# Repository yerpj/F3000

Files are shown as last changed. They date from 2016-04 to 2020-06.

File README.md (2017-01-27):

Power Unit 
----------------

This project aims at designing a generic power IO board for automotive projects

It features:
- 10x 12[V] digital inputs (fully filtered and protected)
- 1x lowside NTC conditionning circuit
- 1x full bridge power output (12V/13A) with temperature protection
- 2x isolated power relay outputs (12V/300mA) with voltage/current spike protection

The headers are meant to be project-agnostic and easy to wire

The interface voltage can be 3.3[V] or 10[V]

More info on demand

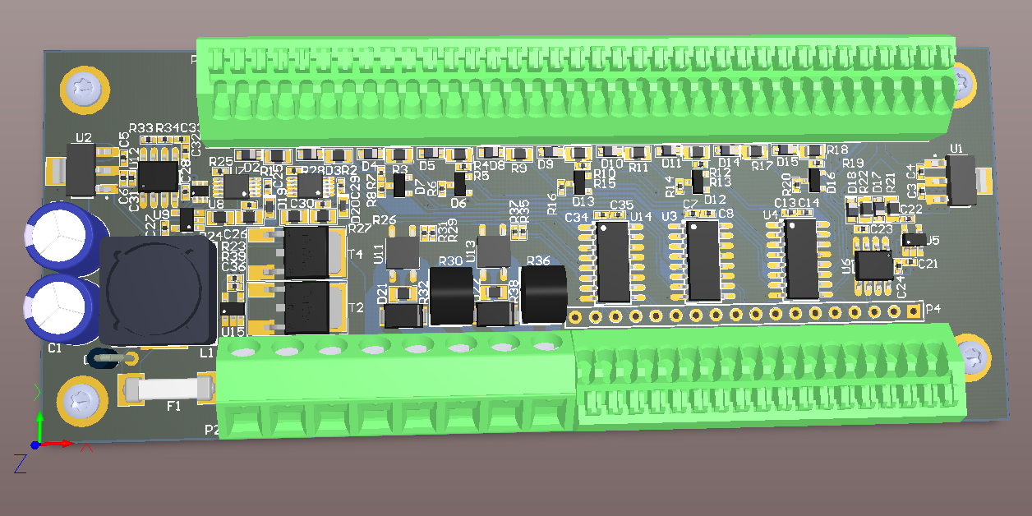
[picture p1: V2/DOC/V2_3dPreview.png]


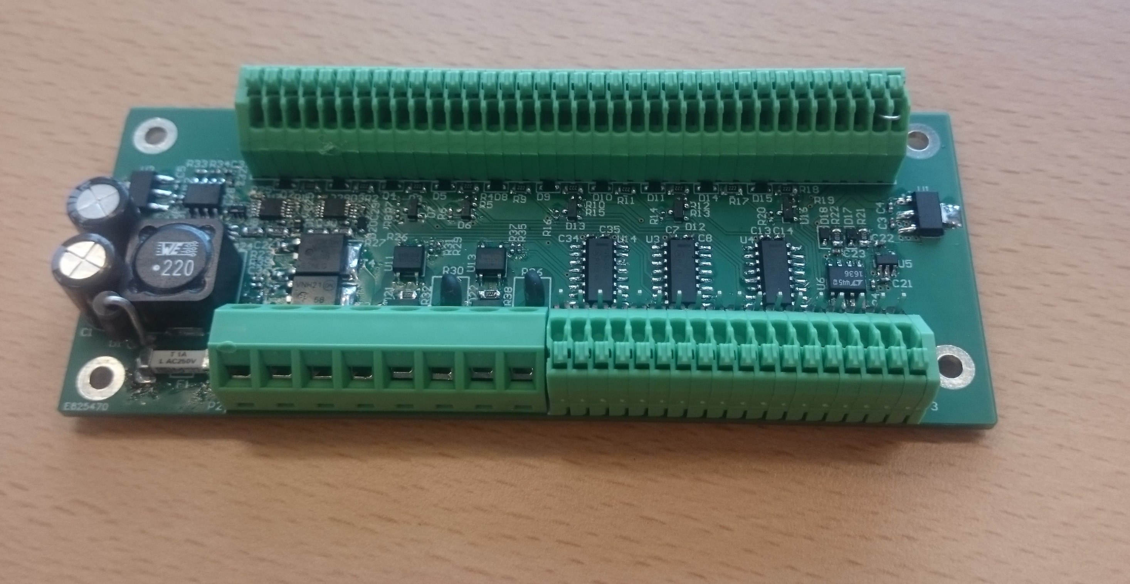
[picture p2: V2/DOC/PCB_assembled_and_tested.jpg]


Control Unit
----------------

As an integral part of the steering wheel, this control unit is able to monitor and drive every IO from the Power Unit, as well as the user interface.

It features:
- 10x 12[V] digital inputs 
- 3x digital outputs
- 6x pushbuttons inputs (SW debounced)
- 1x 7-seg display
- 21 LEDs forming a beautiful bargraph-style regime speed indicator
- individual LEDs for motor temperature, oil warning, neutral-position indication and driving mode*

*: The pilot can at any time select the best gear-driving mode:
- manual control: The gearbox is controlled by pallets on the steering wheel, foot-controlled declutching
- semi-automatic: The gearbox is controlled by pallets on the steering wheel, automatic declutching
- automatic: The gearbox is automatically driven according to engine speed for ascending gears engagement, and manually controlled for descending gears engagement

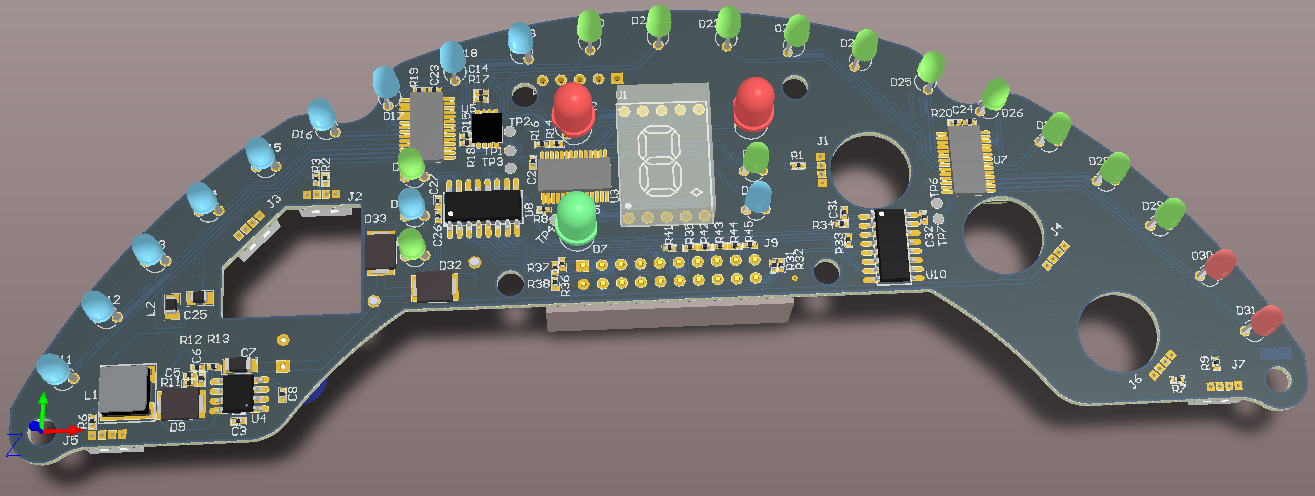
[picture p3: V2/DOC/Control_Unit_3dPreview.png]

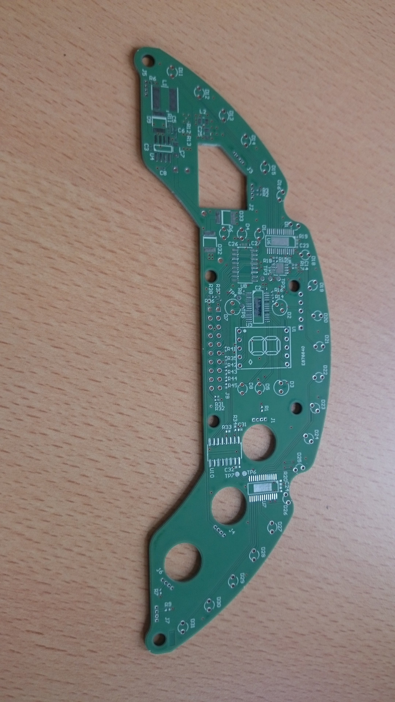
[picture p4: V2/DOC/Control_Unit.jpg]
  
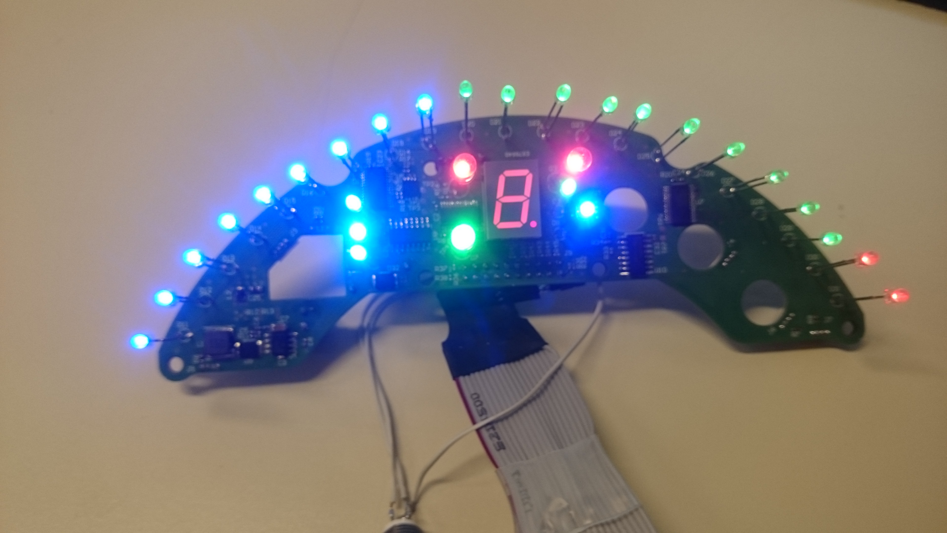
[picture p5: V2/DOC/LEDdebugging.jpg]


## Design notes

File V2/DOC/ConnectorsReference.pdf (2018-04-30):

CU | Spiral cords | PU
Cable | WU side | | PU side | P3 | P1 | P2
"Interface" | wire color | | wire color | "Interface" | "Inputs" | "Outputs"
Pin | Name | left | right | | left | right | Pin | Name | Pin | Name | Pin | Name | Wire
1 | VIN (12V) | | rouge | | | noir | 1 | GND (0V) | 1 | P1 | 1 | STOP+ | 6
2 | GND (0V) | | noir | | | rouge | 2 | VIN (12V) | 2 | GND (0V) | 2 | STOP- | 1
3 | NEUTRE | vert | | | | bleu | 3 | VNTC_out | 3 | VIN (12V) | 3 | START+ | 3
4 | START | jaune | | | | blanc | 4 | Res_out | 4 | P2 | 4 | START- | 1
5 | REGIME | | rose | | | rose | 5 | Regime_out | 5 | GND (0V) | 5 | MOT DC+ | 4
6 | TEMP | | bleu | | | brun | 6 | Huile_out | 6 | VIN (12V) | 6 | MOT DC- | 5
7 | RESERVED1 | | blanc | | blanc | | 7 | Embray_out | 7 | Rapport+ | 7 | VIN (12V) | 1
8 | | | | | rouge | | 8 | Gaz_out | 8 | GND (0V) | 8 | GND (0V) | 2
9 | HUILE | | brun | | vert | | 9 | Neutre_out | 9 | VIN (12V)
10 | EMBRAY | blanc | | | noir | | 10 | Rapport-_out | 10 | Rapport-
11 | SHIFTER | brun | | | rose | | 11 | Rapport+_out | 11 | GND (0V)
12 | CAME | gris | | | brun | | 12 | Shifter_out | 12 | VIN (12V)
13 | RESERVED2 | | gris | | gris | | 13 | Came_out | 13 | Neutre
14 | MOT- | | vert | | | jaune | 14 | Mot+_in | 14 | GND (0V)
15 | RESERVED3 | | | | | vert | 15 | Mot-_in | 15 | VIN (12V)
16 | MOT+ | | jaune | | jaune | | 16 | Relay1_in(Start) | 16 | Gaz
17 | RAPPORT+ | rose | | | bleu | | 17 | Relay2_in(Stop) | 17 | GND (0V)
18 | STOP | bleu | | | | | 18 | | 18 | VIN (12V)
19 | RAPPORT- | noir | | | | | | | 19 | Embray
20 | GAZ | rouge | | | | | | | 20 | GND (0V)
| | | | | | | | | 21 | VIN (12V)
| | | | | | | | | 22 | Huile
| | | | | | | | | 23 | GND (0V)
| | | | | | | | | 24 | VIN (12V)
| | | | | | | | | 25 | Régime
| | | | | | | | | 26 | GND (0V)
| | | | | | | | | 27 | VIN (12V)
| | | | | | | | | 28 | Res_in
| | | | | | | | | 29 | GND (0V)
| | | | | | | | | 30 | VIN (12V)
| | | | | | | | | 31 | NTC
| | | | | | | | | 32 | GND (0V)
| | | | | | | | | 33 | VIN (12V)
| | | | | | | | | 34 | 10V
| | | | | | | | | 35 | VIF
| | | | | | | | | 36 | 3.3V

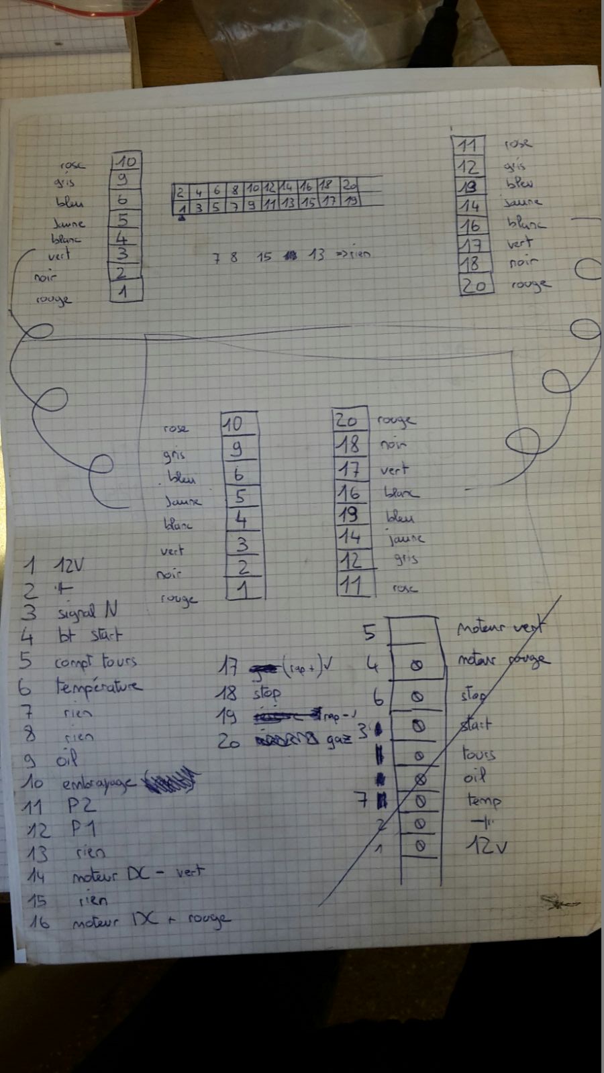
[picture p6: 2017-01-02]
V2/DOC/cablage_notes_julien1.jpg

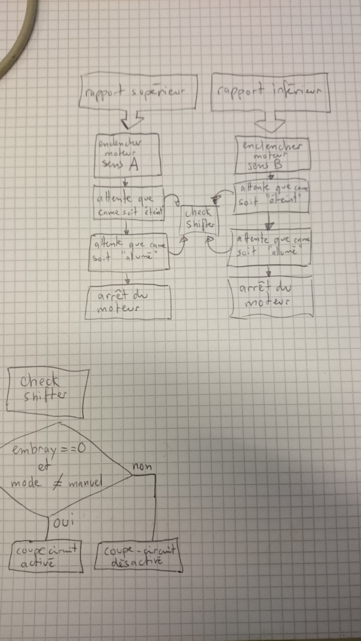
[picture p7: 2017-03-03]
V2/DOC/gear_up_down_procedure.jpeg

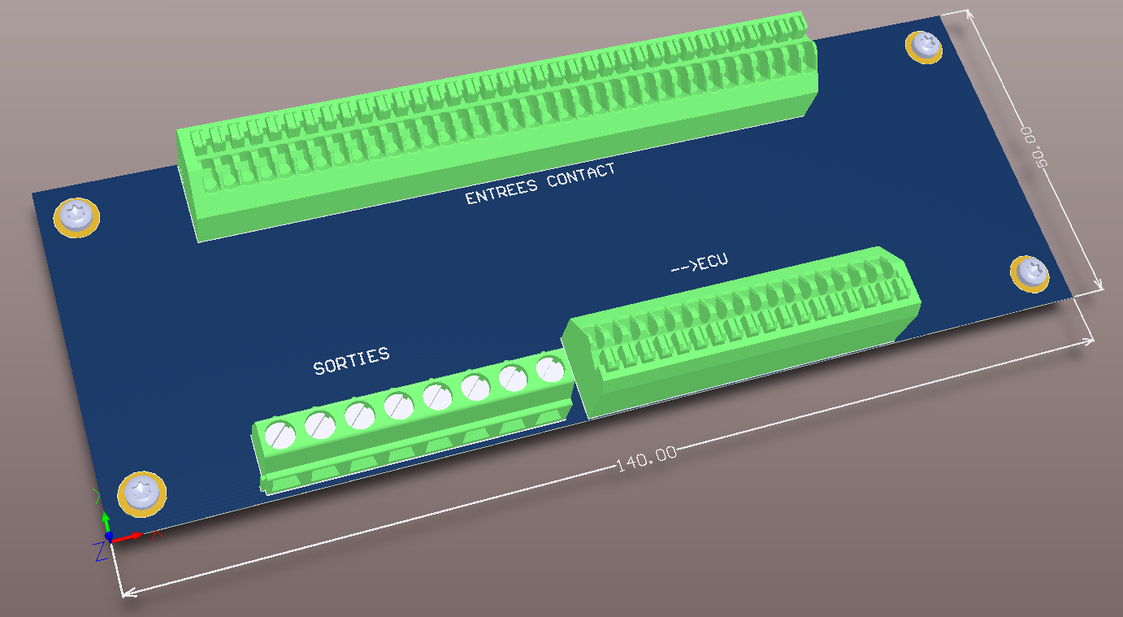
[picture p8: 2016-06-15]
V2/DOC/Capture d'écran 2016-06-15 20.59.19.png

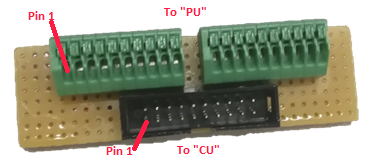
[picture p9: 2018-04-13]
V2/DOC/pics/WU.png

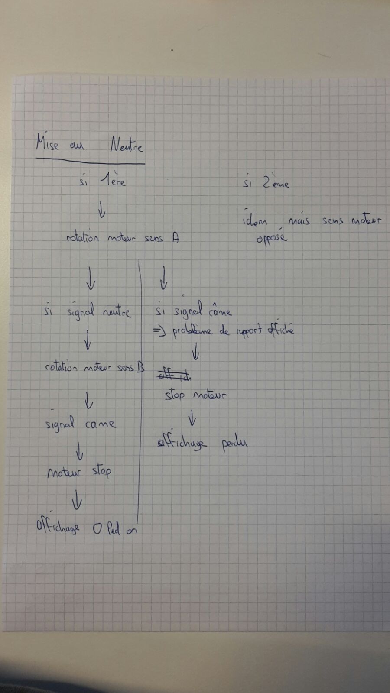
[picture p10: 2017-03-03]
V2/DOC/toNeutral_procedure.jpeg

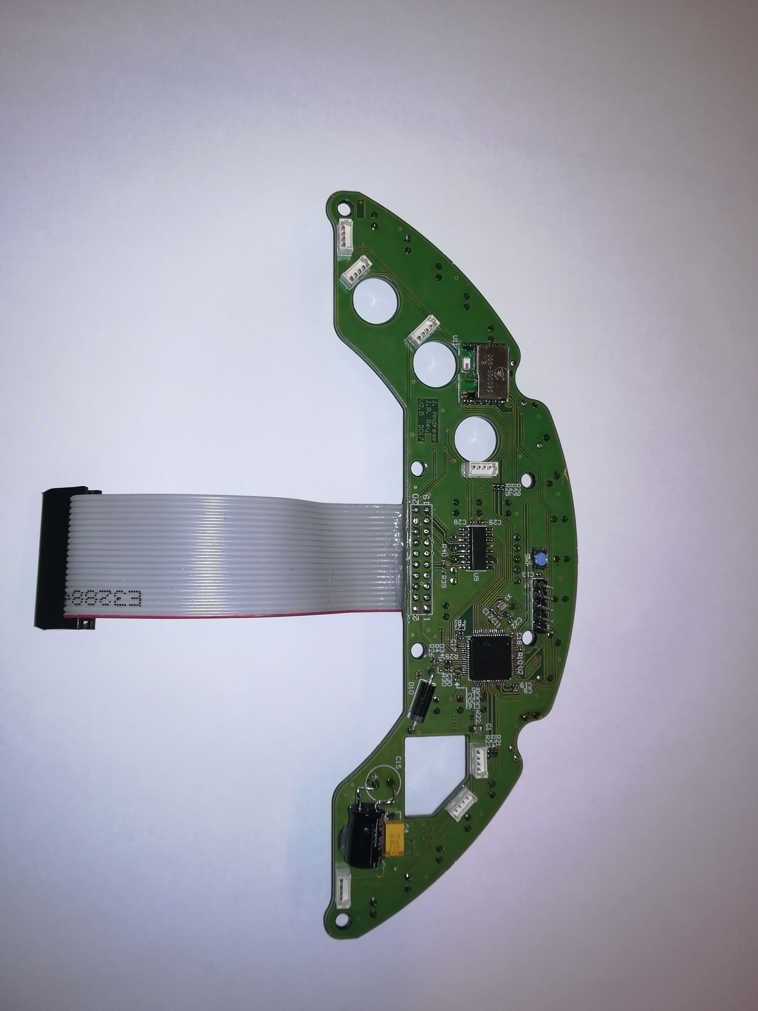
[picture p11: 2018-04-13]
V2/DOC/pics/2018-04-12 16.57.27.jpg

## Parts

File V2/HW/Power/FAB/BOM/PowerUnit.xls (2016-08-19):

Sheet: BOM Report
 |  |  |  | <Parameter Author Field=ProjectName Field=Revision not found>
 |  |  |  | Printed: | 2016-08-19
Index | Designator | Value | Footprint | Manufacturer | Manufacturer PartNum | Quantity
 | C1, C2 | 100u | C_pol8x12mm | Nichicon | UVR1H101MPD1TD | 2
 | C3, C4, C5, C6, C21, C22, C23 | 1u | 0402_ | Murata | GRM155R61E105MA12D | 7
 | C7, C8, C13, C14, C24, C26, C27, C28, C30, C31, C32, C33, C34, C35, C36 | 100n | 0402_ | TDK Corp. | C1005X5R1E104K050BC | 15
 | C9, C10, C11, C12, C15, C16, C17, C18, C19, C20, C37, C38, C39, C40 | 68n | 0603_ | Samsung | CL10B683KB8NNNC | 14
 | C25, C29 | 47n | 0402_ | Murata | GRM155R71H473KE14D | 2
 | D1 |  | R_DIL_vertical_holes1_2mm | ON Semi | 1N5354BG | 1
 | D2, D3, D4, D5, D8, D9, D10, D11, D14, D15, D17, D18 |  | SOD323 | Micro Commercial Co | 1N4148WX-TP | 12
 | D6, D7, D12, D13, D16 |  | SOT23 | Diodes Inc. | AZ23C15-7-F | 5
 | D19, D20 |  | 0603_Pol | Comchip Tech. | CDSU4148 | 2
 | D21, D22 |  | DO-214AC | Littelfuse Inc | SMAJ24CA | 2
 | F1 |  | FUSE_UMT250 | Schurter Inc | 3403.0166.11 | 1
 | L1 | 22u | WURTH_7447709220 | Wurth Electronics Inc | 7447709220 | 1
 | P1 |  | PHOENIX_PTSA05_36 | Phoenix Contact | 1990164 | 1
 | P2 |  | PHOENIX_SMKDSN8 | Phoenix | 1869279 | 1
 | P3 |  | PHOENIX_PTSA05_18 | Phoenix | 1990164 | 1
 | P4 |  | HDR1X18 |  |  | 1
 | R1, R2, R3, R4, R9, R10, R11, R12, R17, R18 | 2k2 | 0805_ | Yageo | RC0805JR-072K2L | 10
 | R5, R6, R7, R8, R13, R14, R15, R16, R19, R20, R31, R33, R37, R39, R40, R41, R42, R43 | 10k | 0402_ | Panasonic | ERJ-2RKF1002X | 18
 | R21, R22 | 500R | 0805_ | Yageo | RC0805FR-07510RL | 2
 | R23, R24, R26, R27 | 22R | 0805_ | Panasonic | ERJ-6ENF22R0V | 4
 | R25, R28 | 100k | 0402_ | Susumu | RR0510P-104-D | 2
 | R29, R35 | 680R | 0402_ | Panasonic | ERJ-2RKF6800X | 2
 | R30, R36 |  | MF72-010D5 | Cantherm | MF72-060D5 | 2
 | R32, R38 | 22k | 0805_ | Rohm Semi | ESR10EZPJ223 | 2
 | R34 | 1k | 0402_ | Rohm Semi | MCR01MRTF1001 | 1
 | T1, T2, T3, T4 |  | DPAK | On Semi | NTD5867NLT4G | 4
 | U1 |  | SOT223-4M | Microchip | MCP1804T-A002I/DB | 1
 | U2 |  | SOT223-4M | Microchip | MCP1804T-3302I/DB | 1
 | U3, U4, U14 |  | SOIC16 | On Semi | MC14504BDG | 3
 | U5 |  | sot23-5 | Microchip | MCP1804T-5002I/OT | 1
 | U6 |  | soic8 | Linear Technology | LT1636CS8#PBF | 1
 | U7, U10 |  | VSSOP10 | Texas Intruments | LM5106MM/NOPB | 2
 | U8 |  | SOT363 | Diodes Inc. | 74LVC1G11DW-7 | 1
 | U9 |  | SOT353 | Diodes Inc. | 74AHC1G32SE-7 | 1
 | U11, U13 |  | CPC10xxN | IXYS Integrated | CPC1018NTR | 2
 | U12 |  | soic8 | Texas Intruments | TLC555CDR | 1
 | U15 |  | SOT23-5 | Microchip | MCP9501PT-095E/OT | 1

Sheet: Project Information
Project Full Path | C:\Users\jeanphil.rey\Documents\JP\Perso\F3000\F3000git\V2\HW\Power\PowerUnit.PrjPCB
Project Filename | PowerUnit.PrjPCB
Variant Name | None
Data-Source Filename | PowerUnit.PrjPCB
Data-Source Full Path | C:\Users\jeanphil.rey\Documents\JP\Perso\F3000\F3000git\V2\HW\Power\PowerUnit.PrjPCB
Title | <Parameter Title not found>
Total Quantity | 130
Report Time | 16:50:49
Report Date | 19.08.2016
Report Date & Tine | 19.08.2016 16:50:49
Output Name | Bill of Materials
Output Type | BOM_PartType
Output Generator Name | BOM
Output Generator Description | Bill of Materials

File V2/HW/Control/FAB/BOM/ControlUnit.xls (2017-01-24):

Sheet: BOM Report
 | Novaccess S.A. Rue Galilée 6 CH-1400 Yverdon-les-Bains | ControlUnit.PrjPCB |  |  |  | Jean-Philippe Rey tel:+41 24 557 27 67
 |  |  |  |  |  | Printed: | 2017-01-24
 |  |  |  |  |  | Quantity: | 2
Entry | Designator | #Column Name Error:value | #Column Name Error:Manufacturer | #Column Name Error:Manufacturer PartNum | Footprint | Digikey ref | Quantity | Expanded Quantity
1 | C1, C25 |  |  |  | 0805_ | 490-10511-1-ND | 2 | 4
2 | C2, C3, C8, C13, C14, C17, C18, C19, C20, C21, C22, C23, C24, C26, C27, C28, C29, C31, C32 |  |  |  | 0402_ | 445-4964-1-ND | 19 | 38
3 | C4 |  |  |  | 2917 | 399-10524-1-ND | 1 | 2
4 | C5, C6 |  |  |  | 0402_ | 1276-1531-1-ND | 2 | 4
5 | C7 |  |  |  | 1206_ | 1276-2876-1-ND | 1 | 2
6 | C9, C10 |  |  |  | 0402_ | 490-10451-1-ND | 2 | 4
7 | C11, C12 |  |  |  | 0402_ | 1276-1608-1-ND | 2 | 4
8 | C15 |  |  |  | C_pol8x12mm | 493-5916-1-ND | 1 | 2
9 | C16, C30 |  |  |  | 0402_ | 490-5915-1-ND | 2 | 4
10 | D1, D5, D6, D20, D21, D22, D23, D24, D25, D26, D27, D28, D29 |  |  |  | LED3MM_GREEN | 754-1915-ND | 13 | 26
11 | D2, D3 |  |  |  | LED5MM_RED | C503B-RCN-CW0Z0AA1-ND | 2 | 4
12 | D4, D8, D11, D12, D13, D14, D15, D16, D17, D18, D19 |  |  |  | LED3MM_BLUE | 732-5011-ND | 11 | 22
13 | D7 |  |  |  | LED5MM_GREEN | 754-1920-ND | 1 | 2
14 | D9, D32, D33 |  |  |  | SMB_FLAT | 497-8036-1-ND | 3 | 6
15 | D10 |  |  |  | 1N5354 | 1N5354BGOS-ND | 1 | 2
16 | D30, D31 |  |  |  | LED3MM_RED | 732-5013-ND | 2 | 4
17 | FB1 |  |  |  | 0402_ | 490-3999-1-ND | 1 | 2
18 | J1, J2, J3, J4, J5, J6, J7 |  |  |  | MOLEX53047-0410 | WM1733-ND | 7 | 14
19 | J8 |  |  |  | HDR1X5 | A9BAG-0502F-ND | 1 | 2
20 | J9 |  |  |  | header2x10 |  | 1 | 2
21 | L1 |  |  |  | SRN6028 | SRN6028-150MCT-ND | 1 | 2
22 | L2 |  |  |  | 0805_ | 587-2903-1-ND | 1 | 2
23 | R1, R2, R3, R6, R7, R9 |  |  |  | 0402_ | RHM1.00KCDCT-ND | 6 | 12
24 | R5, R10, R31, R32, R33, R34, R35, R36, R37, R38, R39, R40, R41, R42, R43, R44, R45 |  |  |  | 0402_ | RR05P10.0KDCT-ND | 17 | 34
25 | R8, R19, R20 |  |  |  | 0402_ | 311-3KLRCT-ND | 3 | 6
26 | R11 |  |  |  | 0402_ | P27.0KLCT-ND | 1 | 2
27 | R12, R14, R15, R16, R17, R18 |  |  |  | 0402_ | P10.0KLCT-ND | 6 | 12
28 | R13 |  |  |  | 0402_ | P3.30KLCT-ND | 1 | 2
29 | R21, R22, R23, R24, R25, R27, R28 |  |  |  | 0402_ | 311-330JRCT-ND | 7 | 14
30 | R29 |  |  |  | 0402_ | 311-1.80KLRCT-ND | 1 | 2
31 | R30 |  |  |  | 0402_ | 311-3.30KLRCT-ND | 1 | 2
32 | SW1 |  |  |  | microswitch_PTS810 | CKN10502CT-ND | 1 | 2
33 | U1 |  |  |  | TDSR1350 | TDSR1350-ND | 1 | 2
34 | U2 |  |  |  | LQFP64 | 497-11154-ND | 1 | 2
35 | U3, U6, U7 |  |  |  | HTSSOP28 | 568-10954-1-ND | 3 | 6
36 | U4 |  |  |  | soic8 | 296-23902-1-ND | 1 | 2
37 | U5 |  |  |  | USON_8L | 1092-1056-ND | 1 | 2
38 | U8, U9, U10 |  |  |  | SOIC16 | MC14504BDGOS-ND | 3 | 6
39 | U11 |  |  |  | SPBT2632C2A | 497-13189-ND | 1 | 2
40 | X1 |  |  |  | FA_128 | 887-2000-1-ND | 1 | 2
41 |  |  |  |  |  |  |  | 0
42 |  |  |  |  |  |  |  | 0
43 |  |  |  |  |  |  |  | 0
44 |  |  |  |  |  |  |  | 0
45 |  |  |  |  |  |  |  | 0
46 |  |  |  |  |  |  |  | 0
47 |  |  |  |  |  |  |  | 0
48 |  |  |  |  |  |  |  | 0
49 |  |  |  |  |  |  |  | 0
50 |  |  |  |  |  |  |  | 0
51 |  |  |  |  |  |  |  | 0
52 |  |  |  |  |  |  |  | 0
53 |  |  |  |  |  |  |  | 0
54 |  |  |  |  |  |  |  | 0
55 |  |  |  |  |  |  |  | 0
56 |  |  |  |  |  |  |  | 0
57 |  |  |  |  |  |  |  | 0
58 |  |  |  |  |  |  |  | 0
59 |  |  |  |  |  |  |  | 0
60 |  |  |  |  |  |  |  | 0
61 |  |  |  |  |  |  |  | 0
62 |  |  |  |  |  |  |  | 0
63 |  |  |  |  |  |  |  | 0
64 |  |  |  |  |  |  |  | 0
65 |  |  |  |  |  |  |  | 0
66 |  |  |  |  |  |  |  | 0
67 |  |  |  |  |  |  |  | 0
68 |  |  |  |  |  |  |  | 0
69 |  |  |  |  |  |  |  | 0
70 |  |  |  |  |  |  |  | 0
71 |  |  |  |  |  |  |  | 0
72 |  |  |  |  |  |  |  | 0
73 |  |  |  |  |  |  |  | 0
74 |  |  |  |  |  |  |  | 0
75 |  |  |  |  |  |  |  | 0
76 |  |  |  |  |  |  |  | 0
77 |  |  |  |  |  |  |  | 0
78 |  |  |  |  |  |  |  | 0
79 |  |  |  |  |  |  |  | 0
80 |  |  |  |  |  |  |  | 0
81 |  |  |  |  |  |  |  | 0
82 |  |  |  |  |  |  |  | 0
83 |  |  |  |  |  |  |  | 0
84 |  |  |  |  |  |  |  | 0
85 |  |  |  |  |  |  |  | 0
86 |  |  |  |  |  |  |  | 0
87 |  |  |  |  |  |  |  | 0
88 |  |  |  |  |  |  |  | 0
89 |  |  |  |  |  |  |  | 0
90 |  |  |  |  |  |  |  | 0
91 |  |  |  |  |  |  |  | 0
92 |  |  |  |  |  |  |  | 0
93 |  |  |  |  |  |  |  | 0
94 |  |  |  |  |  |  |  | 0
95 |  |  |  |  |  |  |  | 0
96 |  |  |  |  |  |  |  | 0
97 |  |  |  |  |  |  |  | 0
98 |  |  |  |  |  |  |  | 0
99 |  |  |  |  |  |  |  | 0
100 |  |  |  |  |  |  |  | 0
101 |  |  |  |  |  |  |  | 0
102 |  |  |  |  |  |  |  | 0
103 |  |  |  |  |  |  |  | 0
104 |  |  |  |  |  |  |  | 0
105 |  |  |  |  |  |  |  | 0
106 |  |  |  |  |  |  |  | 0
107 |  |  |  |  |  |  |  | 0
108 |  |  |  |  |  |  |  | 0
109 |  |  |  |  |  |  |  | 0
110 |  |  |  |  |  |  |  | 0
111 |  |  |  |  |  |  |  | 0
112 |  |  |  |  |  |  |  | 0
113 |  |  |  |  |  |  |  | 0
114 |  |  |  |  |  |  |  | 0
115 |  |  |  |  |  |  |  | 0
116 |  |  |  |  |  |  |  | 0
117 |  |  |  |  |  |  |  | 0
118 |  |  |  |  |  |  |  | 0
119 |  |  |  |  |  |  |  | 0
120 |  |  |  |  |  |  |  | 0
121 |  |  |  |  |  |  |  | 0
122 |  |  |  |  |  |  |  | 0
123 |  |  |  |  |  |  |  | 0
124 |  |  |  |  |  |  |  | 0
125 |  |  |  |  |  |  |  | 0
126 |  |  |  |  |  |  |  | 0
127 |  |  |  |  |  |  |  | 0
128 |  |  |  |  |  |  |  | 0
129 |  |  |  |  |  |  |  | 0
130 |  |  |  |  |  |  |  | 0
131 |  |  |  |  |  |  |  | 0
132 |  |  |  |  |  |  |  | 0
133 |  |  |  |  |  |  |  | 0
134 |  |  |  |  |  |  |  | 0
135 |  |  |  |  |  |  |  | 0
136 |  |  |  |  |  |  |  | 0
137 |  |  |  |  |  |  |  | 0
138 |  |  |  |  |  |  |  | 0
139 |  |  |  |  |  |  |  | 0
140 |  |  |  |  |  |  |  | 0
141 |  |  |  |  |  |  |  | 0
142 |  |  |  |  |  |  |  | 0
143 |  |  |  |  |  |  |  | 0
144 |  |  |  |  |  |  |  | 0
145 |  |  |  |  |  |  |  | 0
146 |  |  |  |  |  |  |  | 0
147 |  |  |  |  |  |  |  | 0
148 |  |  |  |  |  |  |  | 0
149 |  |  |  |  |  |  |  | 0
150 |  |  |  |  |  |  |  | 0
151 |  |  |  |  |  |  |  | 0
152 |  |  |  |  |  |  |  | 0
153 |  |  |  |  |  |  |  | 0
154 |  |  |  |  |  |  |  | 0
155 |  |  |  |  |  |  |  | 0
156 |  |  |  |  |  |  |  | 0
157 |  |  |  |  |  |  |  | 0
158 |  |  |  |  |  |  |  | 0
159 |  |  |  |  |  |  |  | 0
160 |  |  |  |  |  |  |  | 0
161 |  |  |  |  |  |  |  | 0
162 |  |  |  |  |  |  |  | 0
163 |  |  |  |  |  |  |  | 0
164 |  |  |  |  |  |  |  | 0
165 |  |  |  |  |  |  |  | 0
166 |  |  |  |  |  |  |  | 0
167 |  |  |  |  |  |  |  | 0
168 |  |  |  |  |  |  |  | 0
169 |  |  |  |  |  |  |  | 0
170 |  |  |  |  |  |  |  | 0
171 |  |  |  |  |  |  |  | 0
172 |  |  |  |  |  |  |  | 0
173 |  |  |  |  |  |  |  | 0
174 |  |  |  |  |  |  |  | 0
175 |  |  |  |  |  |  |  | 0
176 |  |  |  |  |  |  |  | 0
177 |  |  |  |  |  |  |  | 0
178 |  |  |  |  |  |  |  | 0
179 |  |  |  |  |  |  |  | 0
180 |  |  |  |  |  |  |  | 0
181 |  |  |  |  |  |  |  | 0
182 |  |  |  |  |  |  |  | 0
183 |  |  |  |  |  |  |  | 0
184 |  |  |  |  |  |  |  | 0
185 |  |  |  |  |  |  |  | 0
186 |  |  |  |  |  |  |  | 0
187 |  |  |  |  |  |  |  | 0
188 |  |  |  |  |  |  |  | 0
189 |  |  |  |  |  |  |  | 0
190 |  |  |  |  |  |  |  | 0
191 |  |  |  |  |  |  |  | 0
192 |  |  |  |  |  |  |  | 0
193 |  |  |  |  |  |  |  | 0
194 |  |  |  |  |  |  |  | 0
195 |  |  |  |  |  |  |  | 0
196 |  |  |  |  |  |  |  | 0
197 |  |  |  |  |  |  |  | 0
198 |  |  |  |  |  |  |  | 0
199 |  |  |  |  |  |  |  | 0
200 |  |  |  |  |  |  |  | 0
201 |  |  |  |  |  |  |  | 0
202 |  |  |  |  |  |  |  | 0
203 |  |  |  |  |  |  |  | 0
204 |  |  |  |  |  |  |  | 0
205 |  |  |  |  |  |  |  | 0
206 |  |  |  |  |  |  |  | 0
207 |  |  |  |  |  |  |  | 0
208 |  |  |  |  |  |  |  | 0
209 |  |  |  |  |  |  |  | 0
210 |  |  |  |  |  |  |  | 0
211 |  |  |  |  |  |  |  | 0
212 |  |  |  |  |  |  |  | 0
213 |  |  |  |  |  |  |  | 0
214 |  |  |  |  |  |  |  | 0
215 |  |  |  |  |  |  |  | 0
216 |  |  |  |  |  |  |  | 0
217 |  |  |  |  |  |  |  | 0
218 |  |  |  |  |  |  |  | 0
219 |  |  |  |  |  |  |  | 0
220 |  |  |  |  |  |  |  | 0
221 |  |  |  |  |  |  |  | 0
222 |  |  |  |  |  |  |  | 0
223 |  |  |  |  |  |  |  | 0
224 |  |  |  |  |  |  |  | 0
225 |  |  |  |  |  |  |  | 0
226 |  |  |  |  |  |  |  | 0
227 |  |  |  |  |  |  |  | 0
228 |  |  |  |  |  |  |  | 0
229 |  |  |  |  |  |  |  | 0
230 |  |  |  |  |  |  |  | 0
231 |  |  |  |  |  |  |  | 0
232 |  |  |  |  |  |  |  | 0
233 |  |  |  |  |  |  |  | 0
234 |  |  |  |  |  |  |  | 0
235 |  |  |  |  |  |  |  | 0
236 |  |  |  |  |  |  |  | 0
237 |  |  |  |  |  |  |  | 0
238 |  |  |  |  |  |  |  | 0
239 |  |  |  |  |  |  |  | 0
240 |  |  |  |  |  |  |  | 0
241 |  |  |  |  |  |  |  | 0
242 |  |  |  |  |  |  |  | 0
243 |  |  |  |  |  |  |  | 0
244 |  |  |  |  |  |  |  | 0
245 |  |  |  |  |  |  |  | 0
246 |  |  |  |  |  |  |  | 0
247 |  |  |  |  |  |  |  | 0
248 |  |  |  |  |  |  |  | 0
249 |  |  |  |  |  |  |  | 0
250 |  |  |  |  |  |  |  | 0
251 |  |  |  |  |  |  |  | 0
252 |  |  |  |  |  |  |  | 0
253 |  |  |  |  |  |  |  | 0
254 |  |  |  |  |  |  |  | 0
255 |  |  |  |  |  |  |  | 0
256 |  |  |  |  |  |  |  | 0
257 |  |  |  |  |  |  |  | 0
258 |  |  |  |  |  |  |  | 0
259 |  |  |  |  |  |  |  | 0
260 |  |  |  |  |  |  |  | 0
261 |  |  |  |  |  |  |  | 0
262 |  |  |  |  |  |  |  | 0
263 |  |  |  |  |  |  |  | 0
264 |  |  |  |  |  |  |  | 0
265 |  |  |  |  |  |  |  | 0
266 |  |  |  |  |  |  |  | 0
267 |  |  |  |  |  |  |  | 0
268 |  |  |  |  |  |  |  | 0
269 |  |  |  |  |  |  |  | 0
270 |  |  |  |  |  |  |  | 0
271 |  |  |  |  |  |  |  | 0
272 |  |  |  |  |  |  |  | 0
273 |  |  |  |  |  |  |  | 0
274 |  |  |  |  |  |  |  | 0
275 |  |  |  |  |  |  |  | 0
276 |  |  |  |  |  |  |  | 0
277 |  |  |  |  |  |  |  | 0
278 |  |  |  |  |  |  |  | 0
279 |  |  |  |  |  |  |  | 0
280 |  |  |  |  |  |  |  | 0
281 |  |  |  |  |  |  |  | 0
282 |  |  |  |  |  |  |  | 0
283 |  |  |  |  |  |  |  | 0
284 |  |  |  |  |  |  |  | 0
285 |  |  |  |  |  |  |  | 0
286 |  |  |  |  |  |  |  | 0
287 |  |  |  |  |  |  |  | 0
288 |  |  |  |  |  |  |  | 0
289 |  |  |  |  |  |  |  | 0
290 |  |  |  |  |  |  |  | 0
291 |  |  |  |  |  |  |  | 0
292 |  |  |  |  |  |  |  | 0
293 |  |  |  |  |  |  |  | 0
294 |  |  |  |  |  |  |  | 0
295 |  |  |  |  |  |  |  | 0
296 |  |  |  |  |  |  |  | 0
297 |  |  |  |  |  |  |  | 0
298 |  |  |  |  |  |  |  | 0
299 |  |  |  |  |  |  |  | 0
300 |  |  |  |  |  |  |  | 0
301 |  |  |  |  |  |  |  | 0
302 |  |  |  |  |  |  |  | 0
303 |  |  |  |  |  |  |  | 0
304 |  |  |  |  |  |  |  | 0
305 |  |  |  |  |  |  |  | 0
306 |  |  |  |  |  |  |  | 0
307 |  |  |  |  |  |  |  | 0
308 |  |  |  |  |  |  |  | 0
309 |  |  |  |  |  |  |  | 0
310 |  |  |  |  |  |  |  | 0
311 |  |  |  |  |  |  |  | 0
312 |  |  |  |  |  |  |  | 0
313 |  |  |  |  |  |  |  | 0
314 |  |  |  |  |  |  |  | 0
315 |  |  |  |  |  |  |  | 0
316 |  |  |  |  |  |  |  | 0
317 |  |  |  |  |  |  |  | 0
318 |  |  |  |  |  |  |  | 0
319 |  |  |  |  |  |  |  | 0
320 |  |  |  |  |  |  |  | 0
321 |  |  |  |  |  |  |  | 0
322 |  |  |  |  |  |  |  | 0
323 |  |  |  |  |  |  |  | 0
324 |  |  |  |  |  |  |  | 0
325 |  |  |  |  |  |  |  | 0
326 |  |  |  |  |  |  |  | 0
327 |  |  |  |  |  |  |  | 0
328 |  |  |  |  |  |  |  | 0
329 |  |  |  |  |  |  |  | 0
330 |  |  |  |  |  |  |  | 0
331 |  |  |  |  |  |  |  | 0
332 |  |  |  |  |  |  |  | 0
333 |  |  |  |  |  |  |  | 0
334 |  |  |  |  |  |  |  | 0
335 |  |  |  |  |  |  |  | 0
336 |  |  |  |  |  |  |  | 0
337 |  |  |  |  |  |  |  | 0
338 |  |  |  |  |  |  |  | 0
339 |  |  |  |  |  |  |  | 0
340 |  |  |  |  |  |  |  | 0
341 |  |  |  |  |  |  |  | 0
342 |  |  |  |  |  |  |  | 0
343 |  |  |  |  |  |  |  | 0
344 |  |  |  |  |  |  |  | 0
345 |  |  |  |  |  |  |  | 0
346 |  |  |  |  |  |  |  | 0
347 |  |  |  |  |  |  |  | 0
348 |  |  |  |  |  |  |  | 0
349 |  |  |  |  |  |  |  | 0
350 |  |  |  |  |  |  |  | 0
351 |  |  |  |  |  |  |  | 0
352 |  |  |  |  |  |  |  | 0
353 |  |  |  |  |  |  |  | 0
354 |  |  |  |  |  |  |  | 0
355 |  |  |  |  |  |  |  | 0
356 |  |  |  |  |  |  |  | 0
357 |  |  |  |  |  |  |  | 0
358 |  |  |  |  |  |  |  | 0
359 |  |  |  |  |  |  |  | 0
360 |  |  |  |  |  |  |  | 0
361 |  |  |  |  |  |  |  | 0
362 |  |  |  |  |  |  |  | 0
363 |  |  |  |  |  |  |  | 0
364 |  |  |  |  |  |  |  | 0
365 |  |  |  |  |  |  |  | 0
366 |  |  |  |  |  |  |  | 0
367 |  |  |  |  |  |  |  | 0
368 |  |  |  |  |  |  |  | 0
369 |  |  |  |  |  |  |  | 0
370 |  |  |  |  |  |  |  | 0
371 |  |  |  |  |  |  |  | 0
372 |  |  |  |  |  |  |  | 0
373 |  |  |  |  |  |  |  | 0
374 |  |  |  |  |  |  |  | 0
375 |  |  |  |  |  |  |  | 0
376 |  |  |  |  |  |  |  | 0
377 |  |  |  |  |  |  |  | 0
378 |  |  |  |  |  |  |  | 0
379 |  |  |  |  |  |  |  | 0
380 |  |  |  |  |  |  |  | 0
381 |  |  |  |  |  |  |  | 0
382 |  |  |  |  |  |  |  | 0
383 |  |  |  |  |  |  |  | 0
384 |  |  |  |  |  |  |  | 0
385 |  |  |  |  |  |  |  | 0
386 |  |  |  |  |  |  |  | 0
387 |  |  |  |  |  |  |  | 0
388 |  |  |  |  |  |  |  | 0
389 |  |  |  |  |  |  |  | 0
390 |  |  |  |  |  |  |  | 0
391 |  |  |  |  |  |  |  | 0
392 |  |  |  |  |  |  |  | 0
393 |  |  |  |  |  |  |  | 0
394 |  |  |  |  |  |  |  | 0
395 |  |  |  |  |  |  |  | 0
396 |  |  |  |  |  |  |  | 0
397 |  |  |  |  |  |  |  | 0
398 |  |  |  |  |  |  |  | 0
399 |  |  |  |  |  |  |  | 0
400 |  |  |  |  |  |  |  | 0
401 |  |  |  |  |  |  |  | 0
402 |  |  |  |  |  |  |  | 0
403 |  |  |  |  |  |  |  | 0
404 |  |  |  |  |  |  |  | 0
405 |  |  |  |  |  |  |  | 0
406 |  |  |  |  |  |  |  | 0
407 |  |  |  |  |  |  |  | 0
408 |  |  |  |  |  |  |  | 0
409 |  |  |  |  |  |  |  | 0
410 |  |  |  |  |  |  |  | 0
411 |  |  |  |  |  |  |  | 0
412 |  |  |  |  |  |  |  | 0
413 |  |  |  |  |  |  |  | 0
414 |  |  |  |  |  |  |  | 0
415 |  |  |  |  |  |  |  | 0
416 |  |  |  |  |  |  |  | 0
417 |  |  |  |  |  |  |  | 0
418 |  |  |  |  |  |  |  | 0
419 |  |  |  |  |  |  |  | 0
420 |  |  |  |  |  |  |  | 0
421 |  |  |  |  |  |  |  | 0
422 |  |  |  |  |  |  |  | 0
423 |  |  |  |  |  |  |  | 0
424 |  |  |  |  |  |  |  | 0
425 |  |  |  |  |  |  |  | 0
426 |  |  |  |  |  |  |  | 0
427 |  |  |  |  |  |  |  | 0
428 |  |  |  |  |  |  |  | 0
429 |  |  |  |  |  |  |  | 0
430 |  |  |  |  |  |  |  | 0
431 |  |  |  |  |  |  |  | 0
432 |  |  |  |  |  |  |  | 0
433 |  |  |  |  |  |  |  | 0
434 |  |  |  |  |  |  |  | 0
435 |  |  |  |  |  |  |  | 0
436 |  |  |  |  |  |  |  | 0
437 |  |  |  |  |  |  |  | 0
438 |  |  |  |  |  |  |  | 0
439 |  |  |  |  |  |  |  | 0
440 |  |  |  |  |  |  |  | 0
441 |  |  |  |  |  |  |  | 0
442 |  |  |  |  |  |  |  | 0
443 |  |  |  |  |  |  |  | 0
444 |  |  |  |  |  |  |  | 0
445 |  |  |  |  |  |  |  | 0
446 |  |  |  |  |  |  |  | 0
447 |  |  |  |  |  |  |  | 0
448 |  |  |  |  |  |  |  | 0
449 |  |  |  |  |  |  |  | 0
450 |  |  |  |  |  |  |  | 0
451 |  |  |  |  |  |  |  | 0
452 |  |  |  |  |  |  |  | 0
453 |  |  |  |  |  |  |  | 0
454 |  |  |  |  |  |  |  | 0
455 |  |  |  |  |  |  |  | 0
456 |  |  |  |  |  |  |  | 0
457 |  |  |  |  |  |  |  | 0
458 |  |  |  |  |  |  |  | 0
459 |  |  |  |  |  |  |  | 0
460 |  |  |  |  |  |  |  | 0
461 |  |  |  |  |  |  |  | 0
462 |  |  |  |  |  |  |  | 0
463 |  |  |  |  |  |  |  | 0
464 |  |  |  |  |  |  |  | 0
465 |  |  |  |  |  |  |  | 0
466 |  |  |  |  |  |  |  | 0
467 |  |  |  |  |  |  |  | 0
468 |  |  |  |  |  |  |  | 0
469 |  |  |  |  |  |  |  | 0
470 |  |  |  |  |  |  |  | 0
471 |  |  |  |  |  |  |  | 0
472 |  |  |  |  |  |  |  | 0
473 |  |  |  |  |  |  |  | 0
474 |  |  |  |  |  |  |  | 0
475 |  |  |  |  |  |  |  | 0
476 |  |  |  |  |  |  |  | 0
477 |  |  |  |  |  |  |  | 0
478 |  |  |  |  |  |  |  | 0
479 |  |  |  |  |  |  |  | 0
480 |  |  |  |  |  |  |  | 0
481 |  |  |  |  |  |  |  | 0
482 |  |  |  |  |  |  |  | 0
483 |  |  |  |  |  |  |  | 0
484 |  |  |  |  |  |  |  | 0
485 |  |  |  |  |  |  |  | 0
486 |  |  |  |  |  |  |  | 0
487 |  |  |  |  |  |  |  | 0
488 |  |  |  |  |  |  |  | 0
489 |  |  |  |  |  |  |  | 0
490 |  |  |  |  |  |  |  | 0
491 |  |  |  |  |  |  |  | 0
492 |  |  |  |  |  |  |  | 0
493 |  |  |  |  |  |  |  | 0
494 |  |  |  |  |  |  |  | 0
495 |  |  |  |  |  |  |  | 0
496 |  |  |  |  |  |  |  | 0
497 |  |  |  |  |  |  |  | 0
498 |  |  |  |  |  |  |  | 0
499 |  |  |  |  |  |  |  | 0
500 |  |  |  |  |  |  |  | 0
501 |  |  |  |  |  |  |  | 0
502 |  |  |  |  |  |  |  | 0
503 |  |  |  |  |  |  |  | 0
504 |  |  |  |  |  |  |  | 0
505 |  |  |  |  |  |  |  | 0
506 |  |  |  |  |  |  |  | 0
507 |  |  |  |  |  |  |  | 0
508 |  |  |  |  |  |  |  | 0
509 |  |  |  |  |  |  |  | 0
510 |  |  |  |  |  |  |  | 0
511 |  |  |  |  |  |  |  | 0
512 |  |  |  |  |  |  |  | 0
513 |  |  |  |  |  |  |  | 0
514 |  |  |  |  |  |  |  | 0
515 |  |  |  |  |  |  |  | 0
516 |  |  |  |  |  |  |  | 0
517 |  |  |  |  |  |  |  | 0
518 |  |  |  |  |  |  |  | 0
519 |  |  |  |  |  |  |  | 0
520 |  |  |  |  |  |  |  | 0
521 |  |  |  |  |  |  |  | 0
522 |  |  |  |  |  |  |  | 0
523 |  |  |  |  |  |  |  | 0
524 |  |  |  |  |  |  |  | 0
525 |  |  |  |  |  |  |  | 0
526 |  |  |  |  |  |  |  | 0
527 |  |  |  |  |  |  |  | 0
528 |  |  |  |  |  |  |  | 0
529 |  |  |  |  |  |  |  | 0
530 |  |  |  |  |  |  |  | 0
531 |  |  |  |  |  |  |  | 0
532 |  |  |  |  |  |  |  | 0
533 |  |  |  |  |  |  |  | 0
534 |  |  |  |  |  |  |  | 0
535 |  |  |  |  |  |  |  | 0
536 |  |  |  |  |  |  |  | 0
537 |  |  |  |  |  |  |  | 0
538 |  |  |  |  |  |  |  | 0
539 |  |  |  |  |  |  |  | 0
540 |  |  |  |  |  |  |  | 0
541 |  |  |  |  |  |  |  | 0
542 |  |  |  |  |  |  |  | 0
543 |  |  |  |  |  |  |  | 0
544 |  |  |  |  |  |  |  | 0
545 |  |  |  |  |  |  |  | 0
546 |  |  |  |  |  |  |  | 0
547 |  |  |  |  |  |  |  | 0
548 |  |  |  |  |  |  |  | 0
549 |  |  |  |  |  |  |  | 0
550 |  |  |  |  |  |  |  | 0
551 |  |  |  |  |  |  |  | 0
552 |  |  |  |  |  |  |  | 0
553 |  |  |  |  |  |  |  | 0
554 |  |  |  |  |  |  |  | 0
555 |  |  |  |  |  |  |  | 0
556 |  |  |  |  |  |  |  | 0
557 |  |  |  |  |  |  |  | 0
558 |  |  |  |  |  |  |  | 0
559 |  |  |  |  |  |  |  | 0
560 |  |  |  |  |  |  |  | 0
561 |  |  |  |  |  |  |  | 0
562 |  |  |  |  |  |  |  | 0
563 |  |  |  |  |  |  |  | 0
564 |  |  |  |  |  |  |  | 0
565 |  |  |  |  |  |  |  | 0
566 |  |  |  |  |  |  |  | 0
567 |  |  |  |  |  |  |  | 0
568 |  |  |  |  |  |  |  | 0
569 |  |  |  |  |  |  |  | 0
570 |  |  |  |  |  |  |  | 0
571 |  |  |  |  |  |  |  | 0
572 |  |  |  |  |  |  |  | 0
573 |  |  |  |  |  |  |  | 0
574 |  |  |  |  |  |  |  | 0
575 |  |  |  |  |  |  |  | 0
576 |  |  |  |  |  |  |  | 0
577 |  |  |  |  |  |  |  | 0
578 |  |  |  |  |  |  |  | 0
579 |  |  |  |  |  |  |  | 0
580 |  |  |  |  |  |  |  | 0
581 |  |  |  |  |  |  |  | 0
582 |  |  |  |  |  |  |  | 0
583 |  |  |  |  |  |  |  | 0
584 |  |  |  |  |  |  |  | 0
585 |  |  |  |  |  |  |  | 0
586 |  |  |  |  |  |  |  | 0
587 |  |  |  |  |  |  |  | 0
588 |  |  |  |  |  |  |  | 0
589 |  |  |  |  |  |  |  | 0
590 |  |  |  |  |  |  |  | 0
591 |  |  |  |  |  |  |  | 0
592 |  |  |  |  |  |  |  | 0
593 |  |  |  |  |  |  |  | 0
557 |  |  |  |  |  |  |  | 0
558 |  |  |  |  |  |  |  | 0
559 |  |  |  |  |  |  |  | 0
560 |  |  |  |  |  |  |  | 0
561 |  |  |  |  |  |  |  | 0

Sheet: Project Information
Project Full Path | C:\Users\jeanphil.rey\Documents\JP\Perso\F3000\F3000git\V2\HW\Control\ControlUnit.PrjPCB
Project Filename | ControlUnit.PrjPCB
Variant Name | Normal
Data-Source Filename | ControlUnit.PrjPCB
Data-Source Full Path | C:\Users\jeanphil.rey\Documents\JP\Perso\F3000\F3000git\V2\HW\Control\ControlUnit.PrjPCB
Title | <Parameter Title not found>
Total Quantity | 133
Report Time | 19:03:37
Report Date | 24.01.2017
Report Date & Tine | 24.01.2017 19:03:37
Output Name | Bill of Materials
Output Type | BOM_PartType
Output Generator Name | BOM
Output Generator Description | Bill of Materials

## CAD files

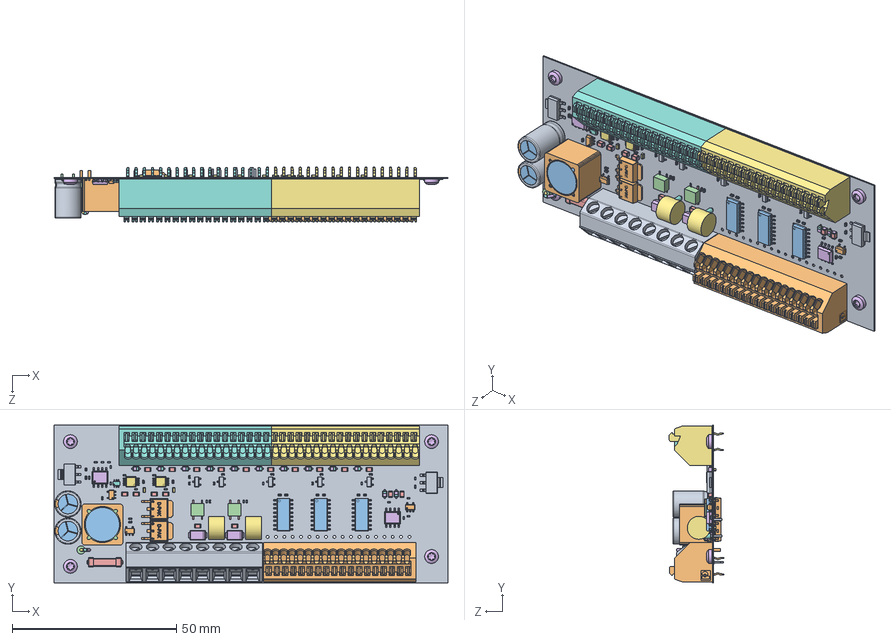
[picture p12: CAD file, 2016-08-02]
V2/HW/Power/CAD/PowerUnit.SLDASM
120.0 x 48.0 x 16.6 mm
Board
sot235_2 x 3
SOIC-16-2 x 3
Extruded x 2
Extruded_2 x 8
soic8 x 2
vssop10 x 2
User_Library-SOT363-2
SOT-223-4 x 2
D-PAK x 4
User_Library-V0402HD_K_X_F6rper_1 x 47
User_Library-V0402HD_Anschl_X_FCsse_1 x 47
User_Library-V0805HD_K_X_F6rper_1 x 18
User_Library-V0805HD_Anschl_X_FCsse_1 x 18
Extruded_3
Extruded_4
UMT250_FUSE
DO-214AC x 2
SW3dPS-SOD-323F_Board5 x 12
SW3dPS-SOD-323F_Extruded9 x 24
SW3dPS-SOD-323F_Board4 x 24
SW3dPS-SOD-323F_Extruded8 x 24
SW3dPS-SOD-323F_Extruded10 x 24
SW3dPS-SOD-323F_Board3 x 24
SW3dPS-SOD-323F_Extruded7 x 12
SW3dPS-SOD-323F_Extruded6 x 12
SW3dPS-SOD-323F_Extruded11 x 12
sot23 x 5
User_Library-Cap_electrolitic_radial_8x12_Case x 2
User_Library-Cap_electrolitic_radial_8x12_Minus x 2
User_Library-Cap_electrolitic_radial_8x12_Top x 2
User_Library-Cap_electrolitic_radial_8x12_Pins x 2
User_Library-Cap_electrolitic_radial_8x12_Bottom x 2
BN_132652_5x6_headonly x 4
ptsa_0.5-18-2.5-z_cut
ptsa_0.5-18-2.5-z
smkdsn_1.5-8-5.08
ptsa_0.5-18-2.5-z_2

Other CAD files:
V2/HW/Power/CAD/R23.sldasm
V2/HW/Power/CAD/C36.sldasm
V2/HW/Power/CAD/C6.sldasm
V2/HW/Power/CAD/R36.sldasm
V2/HW/Power/CAD/C39.sldasm
V2/HW/Power/CAD/D22.sldasm
V2/HW/Power/CAD/C33.sldasm
V2/HW/Power/CAD/R30.sldasm
V2/HW/Power/CAD/R25.sldasm
V2/HW/Power/CAD/C32.sldasm
V2/HW/Power/CAD/U12.sldasm
V2/HW/Power/CAD/R27.sldasm
V2/HW/Power/CAD/D17.sldasm
V2/HW/Power/CAD/R20.sldasm
V2/HW/Power/CAD/U10.sldasm
V2/HW/Power/CAD/R16.sldasm
V2/HW/Power/CAD/C38.sldasm
V2/HW/Control/CAD/ControlUnit.DWG
V2/HW/Control/CAD/PCB_mec.dwg
V2/HW/Control/CAD/boitier/boitier.SLDDRW
V2/HW/Control/CAD/boitier/boitier.SLDPRT
V2/HW/Control/CAD/boitier/boitier.STEP
V2/HW/Control/CAD/boitier/boitier_ledHolesRelaxed.STEP
V2/HW/Control/CAD/boitier/contour_carte.dwg
V2/HW/Control/CAD/boitier/contour_carte.dxf
V2/HW/Control/CAD/control_PCB_outline.dwg
V2/HW/Power/CAD/0402.sldasm
V2/HW/Power/CAD/0603.sldprt
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

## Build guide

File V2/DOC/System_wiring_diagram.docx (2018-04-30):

# Schematic view

Control Unit « CU »

Wiring unit « WU »

Power Unit « PU »

# Elements

## Control Unit

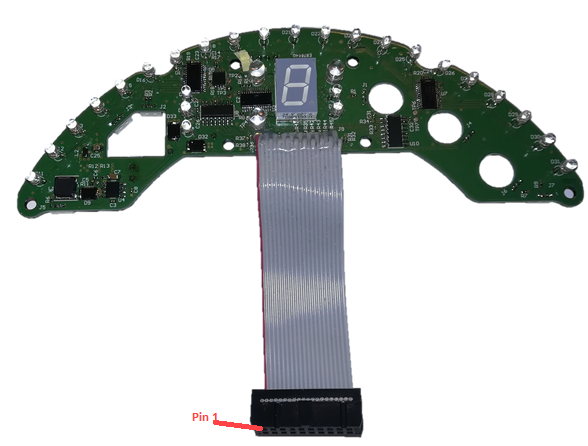
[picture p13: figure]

Figure 1: Control Unit "CU" with its 20-pin flat-cable

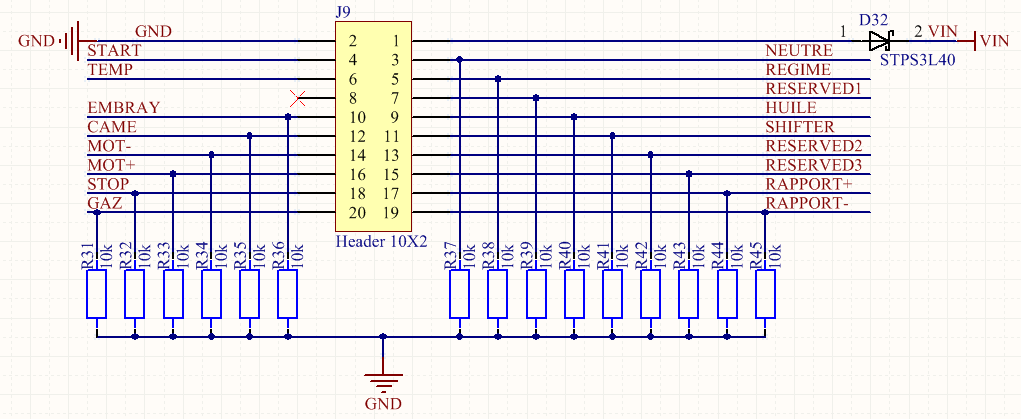
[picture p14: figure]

Figure 2: CU 20-pin header

## Wiring Unit


Figure 3: Wiring Unit "WU"

## Power Unit

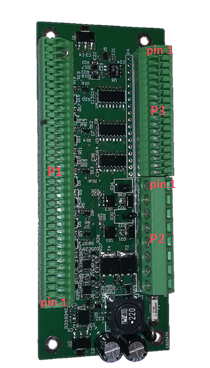
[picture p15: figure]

Figure 4: Power Unit "PU"

# Connectors reference

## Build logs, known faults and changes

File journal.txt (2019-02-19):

19.02.2019		Nappe 20poles mal soudée sur carte CU2. Ressoudage
				vérification fonctionnement CU2 et PU2. Préparation pour laquage
				Laquage PU2 et CU2.

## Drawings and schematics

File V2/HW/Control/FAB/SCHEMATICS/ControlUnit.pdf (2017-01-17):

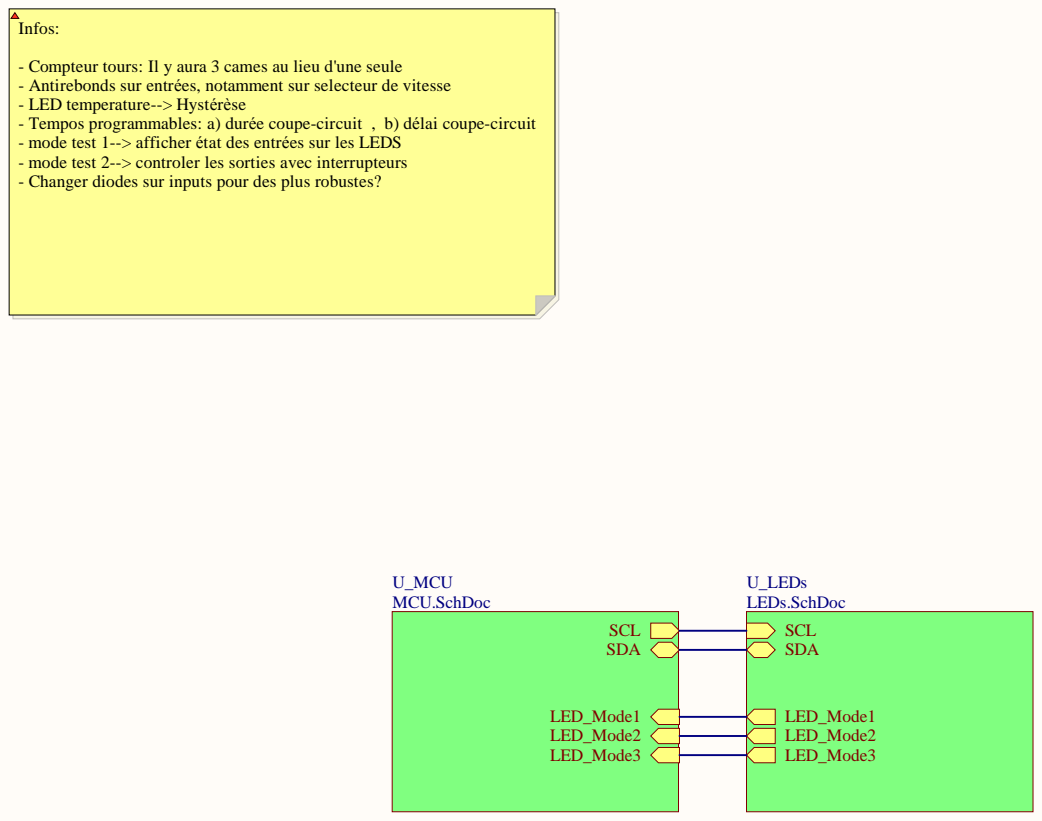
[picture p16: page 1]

- Compteur tours: Il y aura 3 cames au lieu d'une seule
- Antirebonds sur entrées, notamment sur selecteur de vitesse
- LED temperature--> Hystérèse
- Tempos programmables: a) durée coupe-circuit , b) délai coupe-circuit
- mode test 1--> afficher état des entrées sur les LEDS
- mode test 2--> controler les sorties avec interrupteurs
- Changer diodes sur inputs pour des plus robustes?

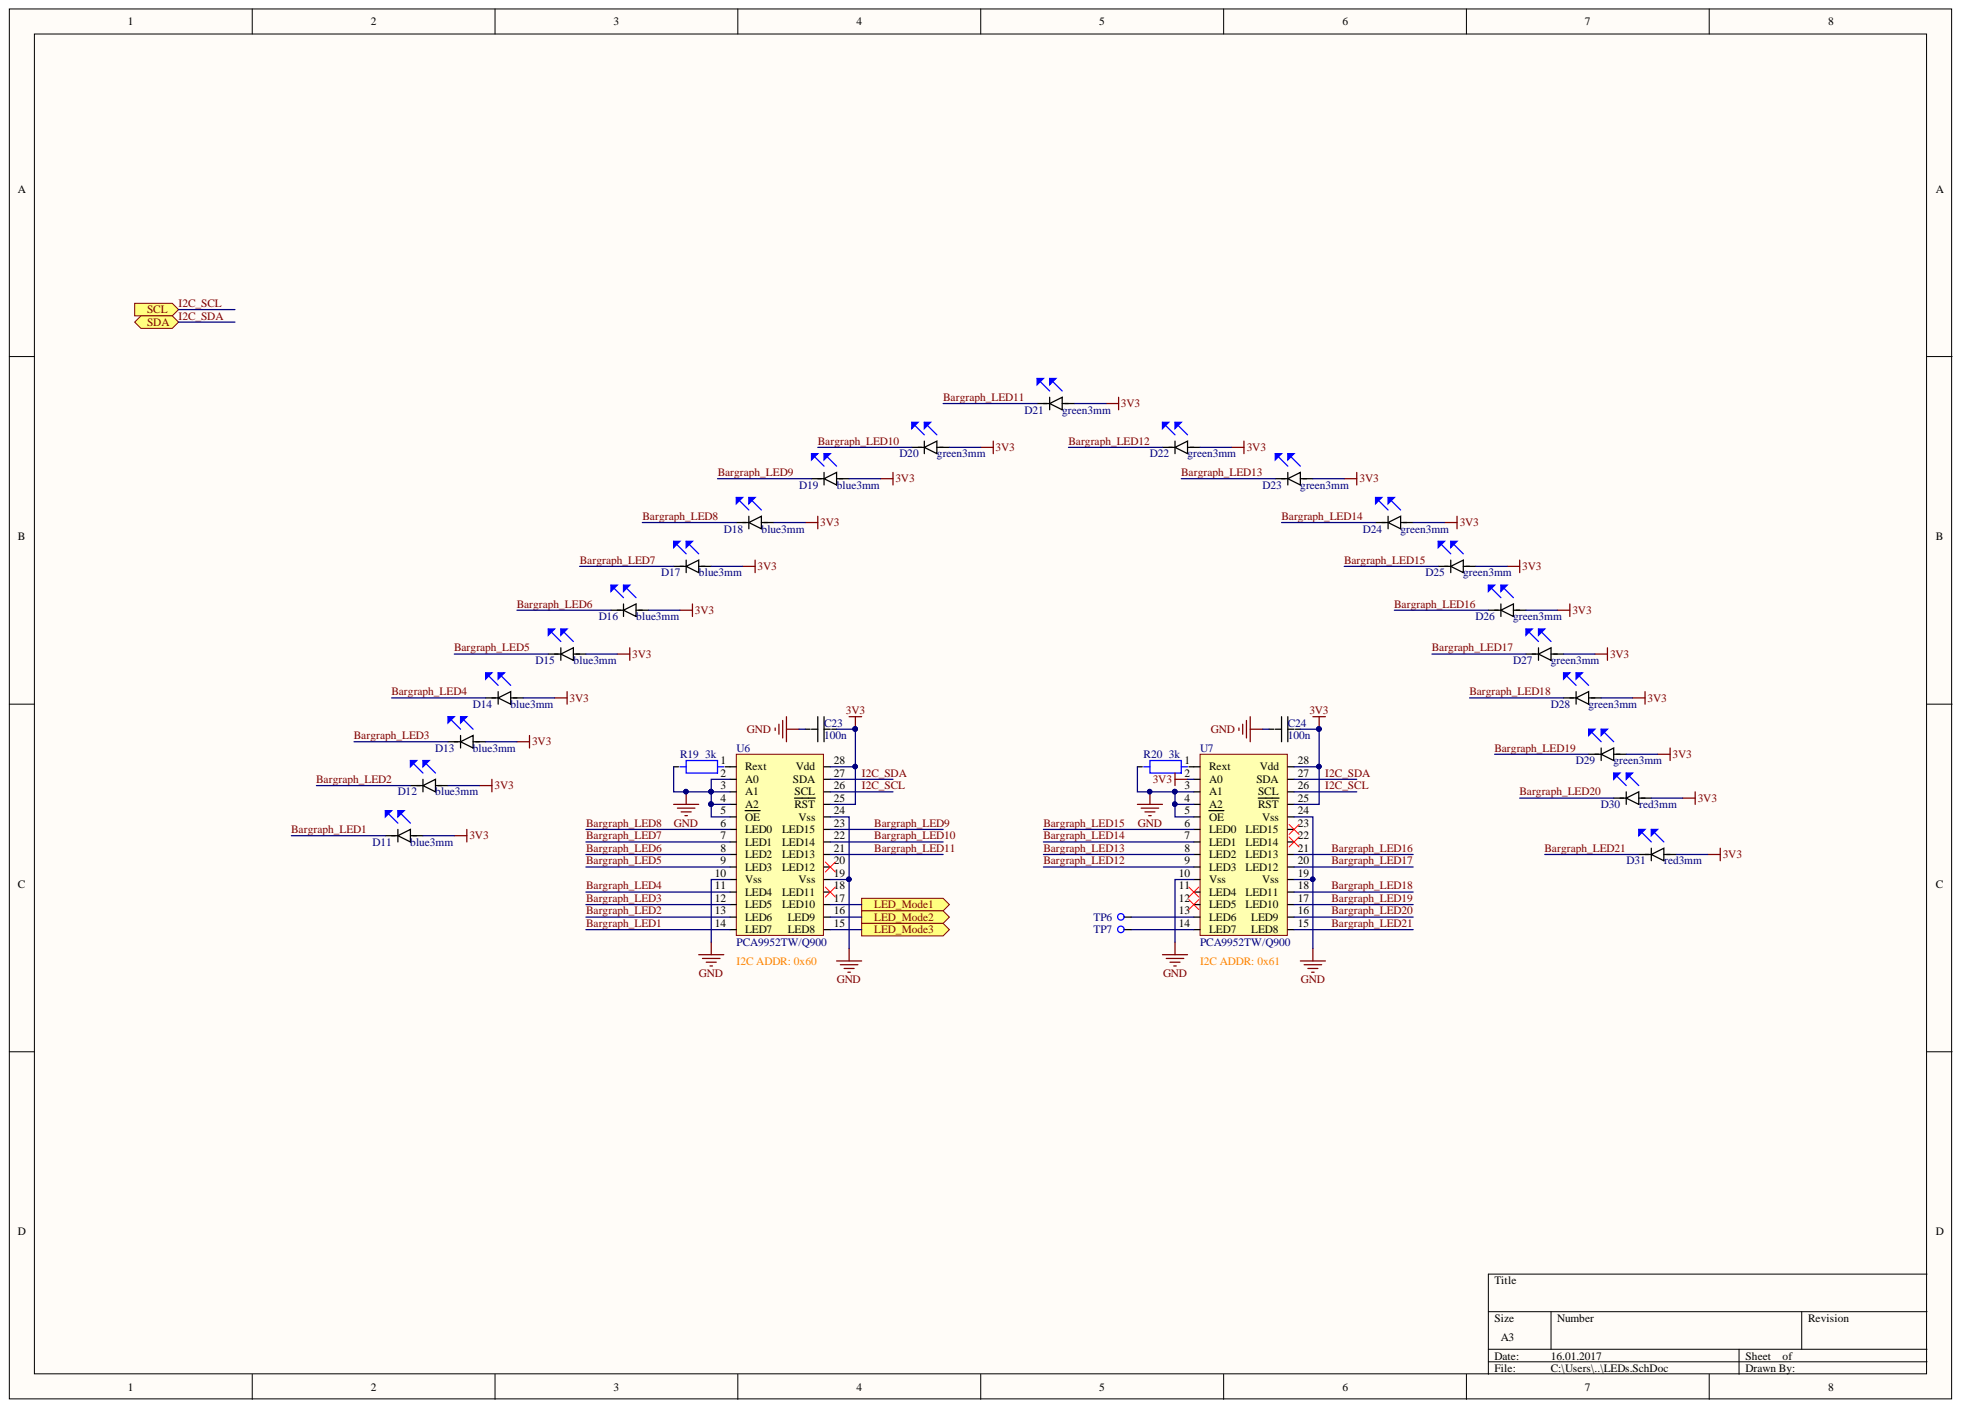
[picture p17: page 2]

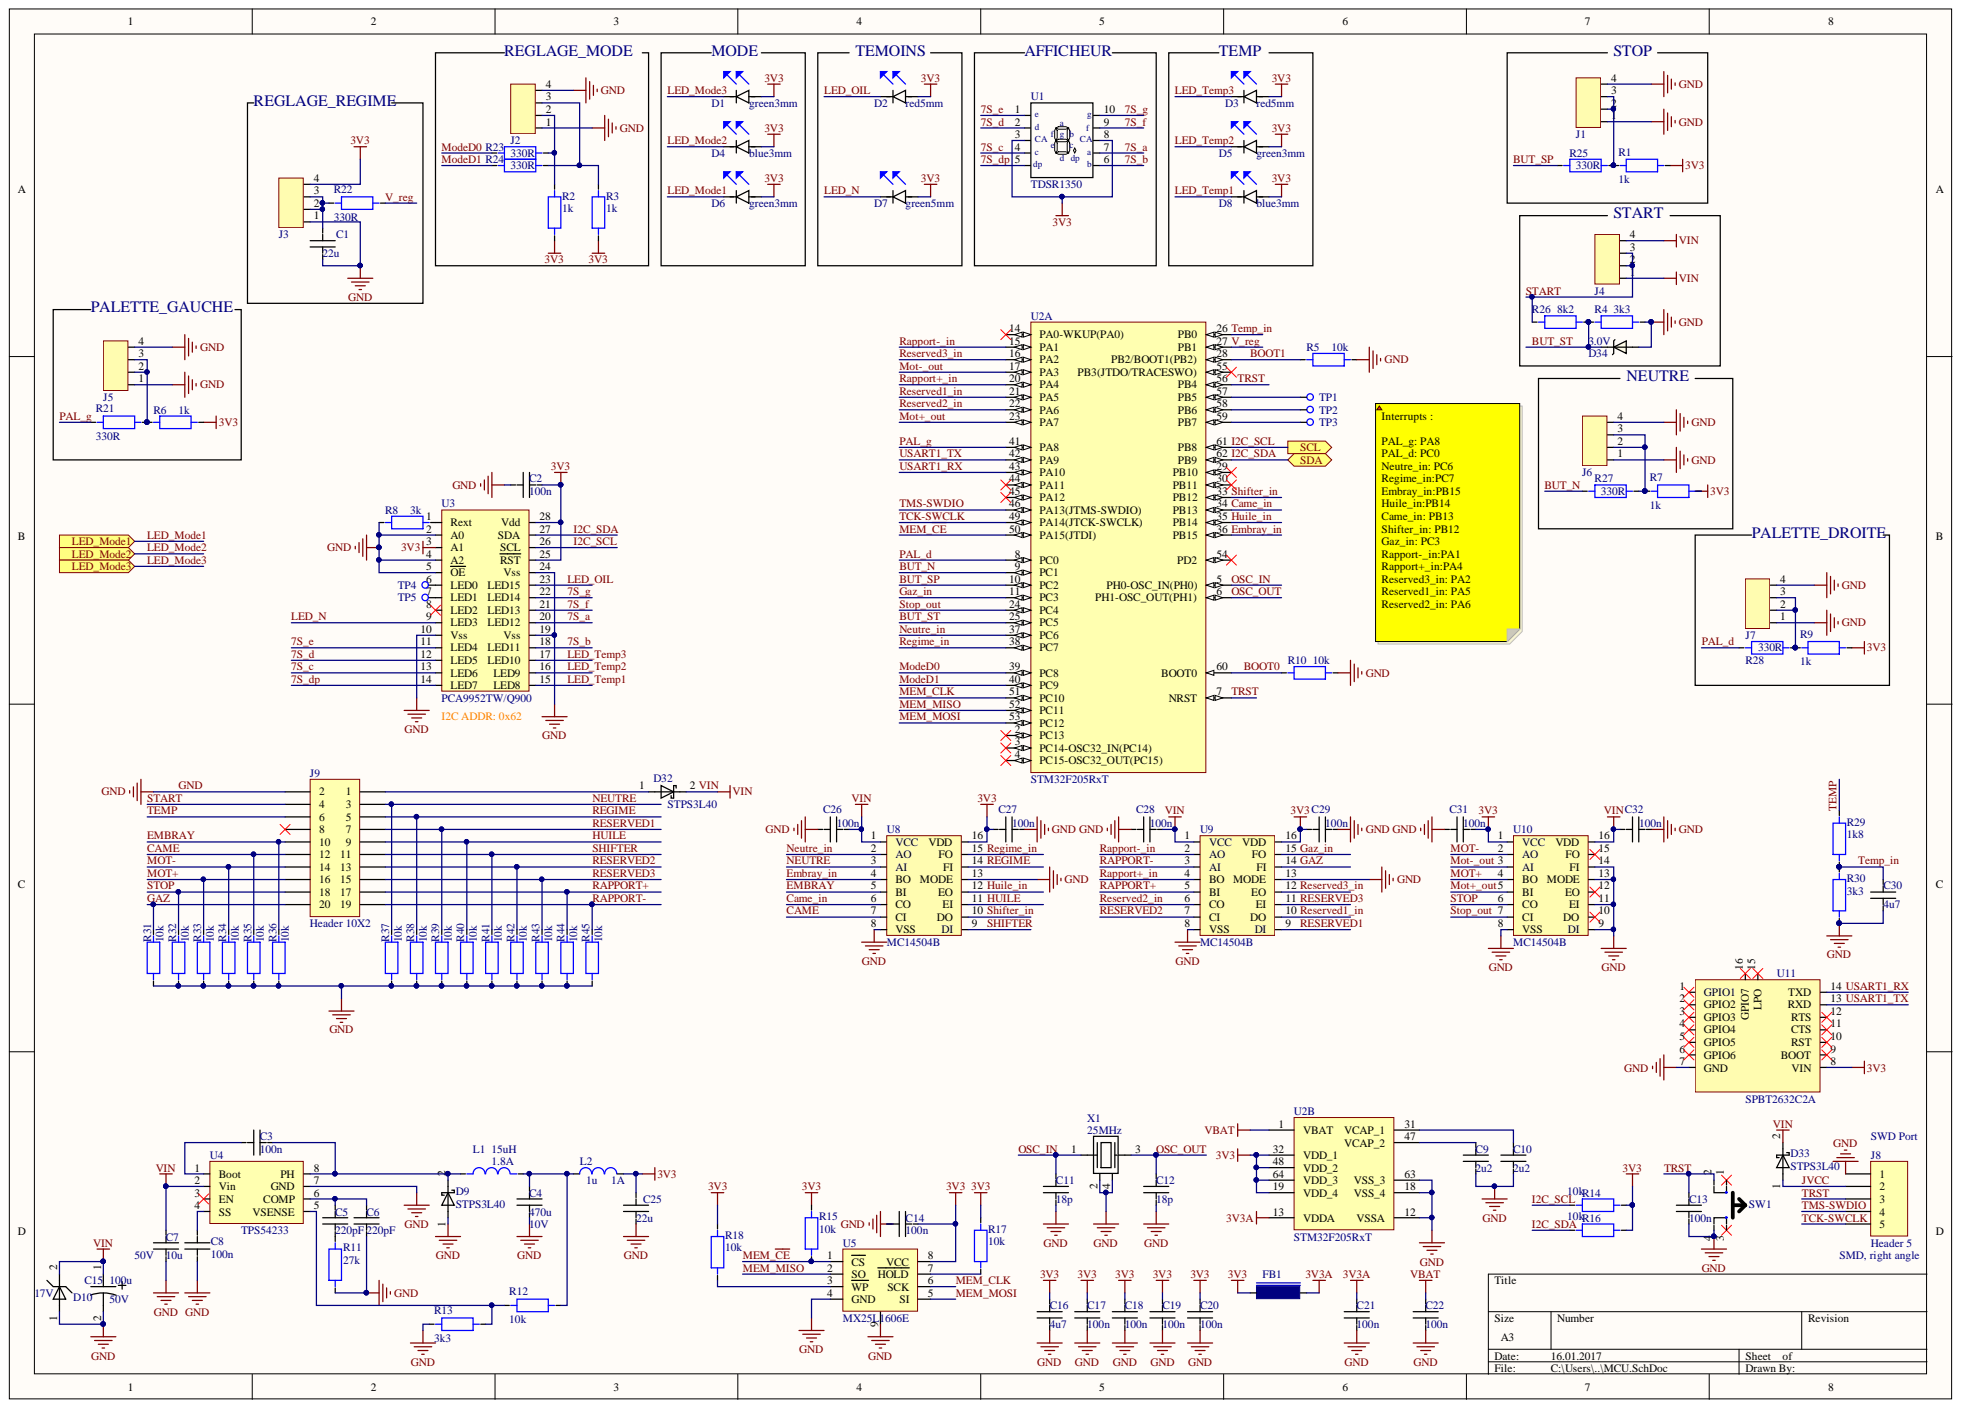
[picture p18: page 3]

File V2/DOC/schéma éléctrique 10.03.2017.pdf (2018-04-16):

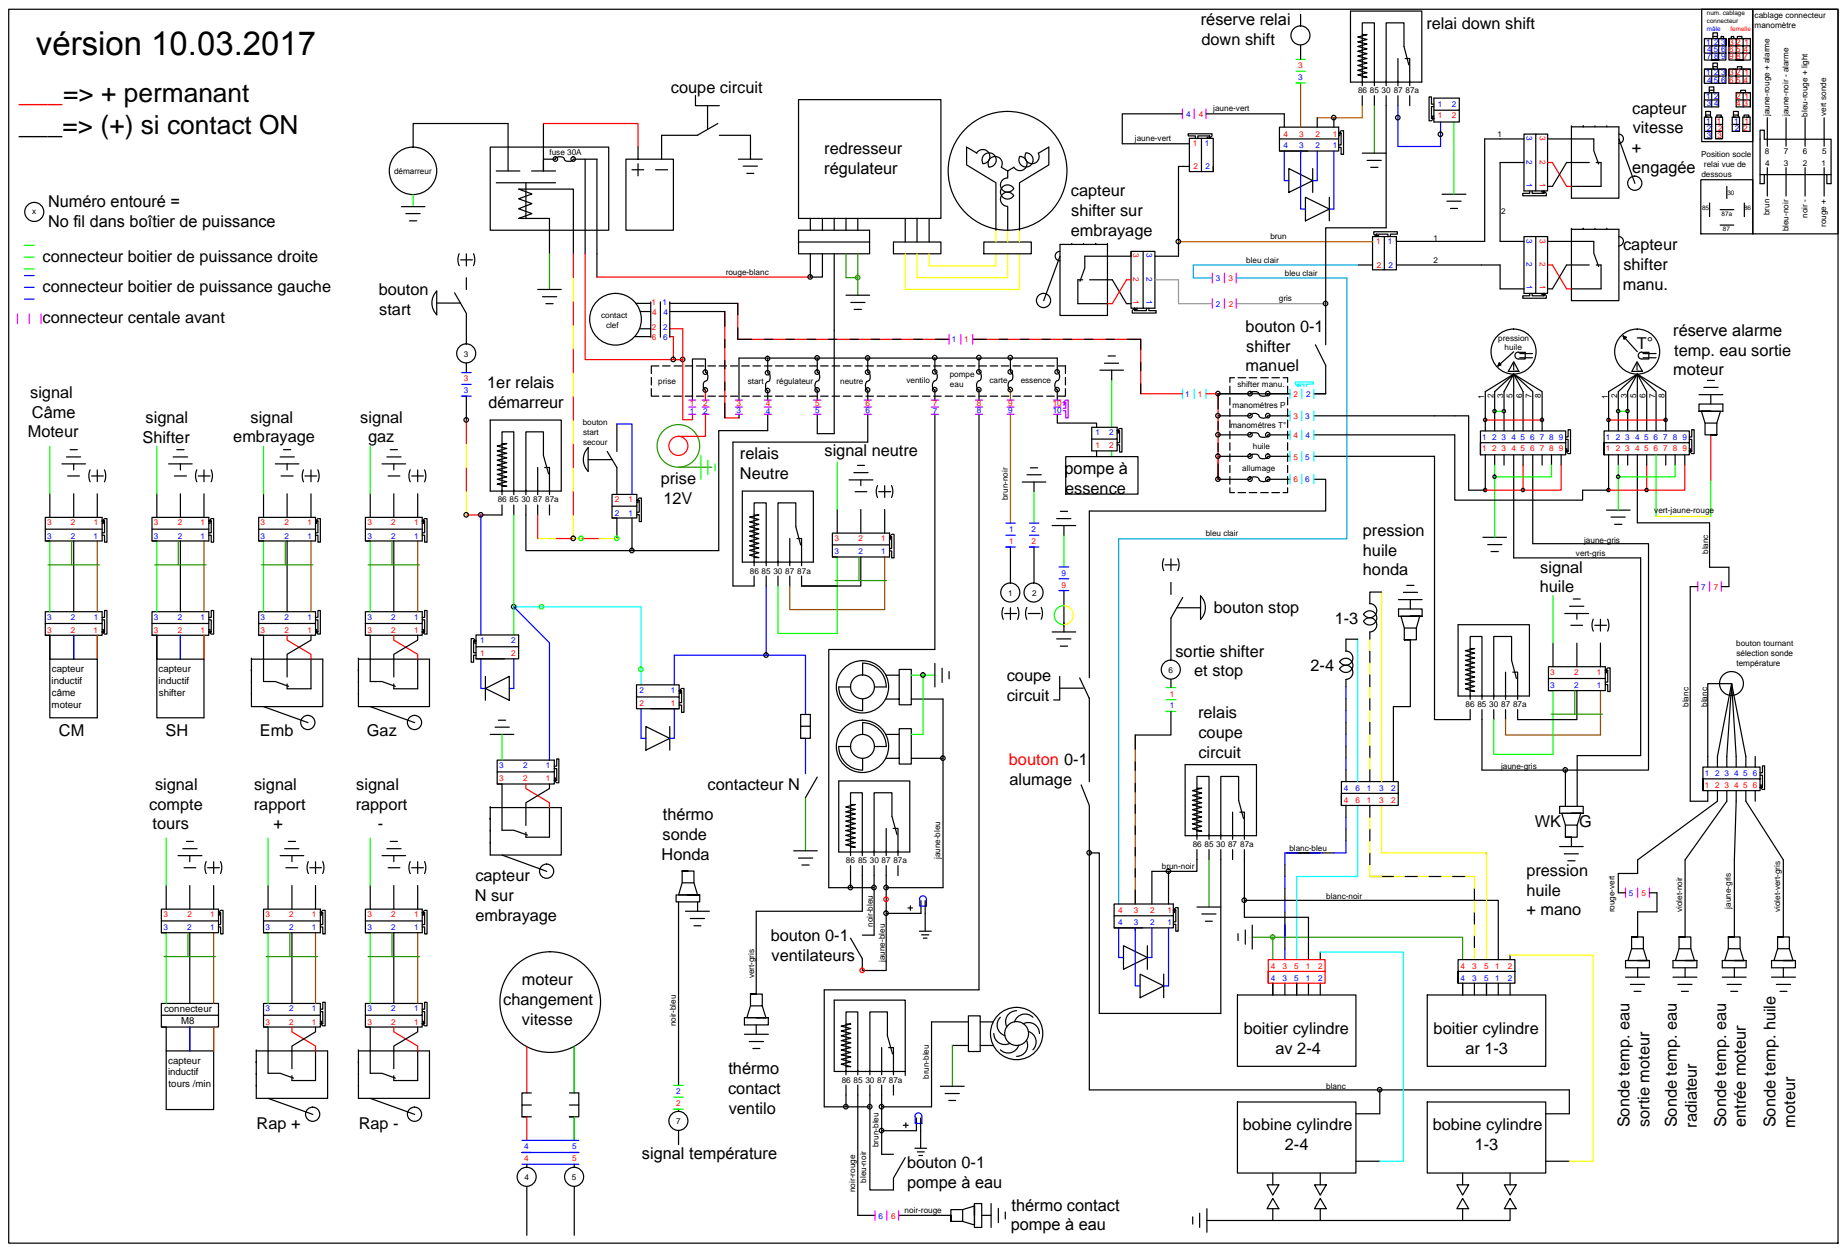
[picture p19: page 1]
contacteur N; 1er relais; boitier cylindre av 2-4; boitier cylindre ar 1-3; circuit bouton 0-1; sortie shifter et stop; bobine cylindre; fuse 30A; bouton stop; bouton 0-1; N sur; Rap +; rapport +; Rap -; rapport -; prise; coupe circuit; tours /min; shifter manu.; start secour; sortie moteur; neutre; essence pompe eau ventilo; shifter sur; bleu clair; down shift; vert sonde; noir -; rouge +; huile + mano; vert-jaune-rouge; blanc 1 2 3; bouton tournant; signal neutre

relai down shift
shifter manu. capteur vitesse +HQJDJpH

num. cablage connecteur PkOH femelle | cablage connecteur PDQRPqWUH

3 2 1
4 5 | 6 6 5 4
7 | 8 9 9 8 7

jaune-rouge + alarme

jaune-noir - alarme

bleu-rouge + light

1 | 2 3 3 2 1

vitesse ___=> + permanant ___=> (+) si contact ON

Position socle
relai vue de
dessous

1RILOGDQVERvWLHUGHSXLVVDQFH

connecteur boitier de puissance droite

connecteur boitier de puissance gauche

connecteur centale avant

UpVHUYHDODUPH
temp. eau sortie
moteur

SRPSHj essence carte prise 12V

8 jaune-gris blanc

violet-vert-gris

bleu-noir noir-bleu

4 3 5 1 2 | 4 3 5 1 2

Sonde temp. huile

Sonde temp. eau

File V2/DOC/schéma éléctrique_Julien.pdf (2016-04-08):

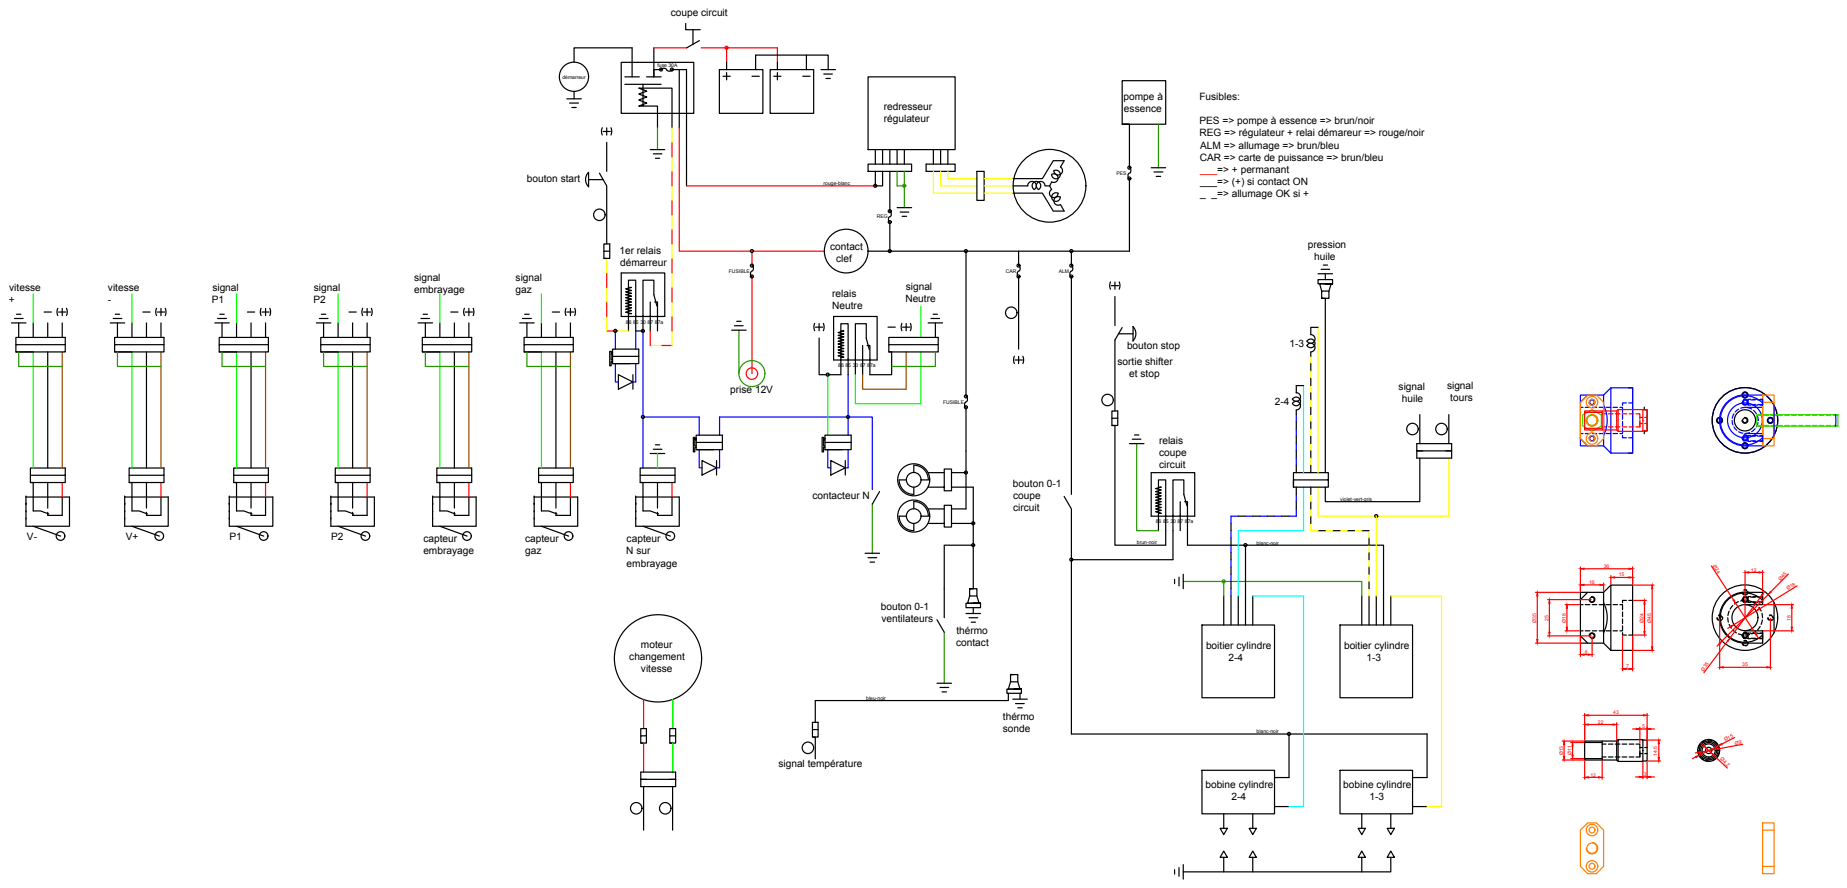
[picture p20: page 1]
contacteur N 86 85 30 87 87a 1er relais démarreur; 86 85 30 87 87a relais Neutre; signal Neutre; boitier cylindre 2-4; boitier cylindre 1-3 86 85 30 87 87a relais coupe circuit bouton 0-1 coupe circuit bouton start; sortie shifter et stop; bobine cylindre 2-4; bobine cylindre 1-3; signal huile; signal tours brun-noir; blanc-noir blanc-noir2-41-3 pression huile fuse 30A démarreur; rouge-blanc; redresseur régulateur REG; ALM; bouton stop contact clef; bouton 0-1 ventilateurs; thérmo contact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

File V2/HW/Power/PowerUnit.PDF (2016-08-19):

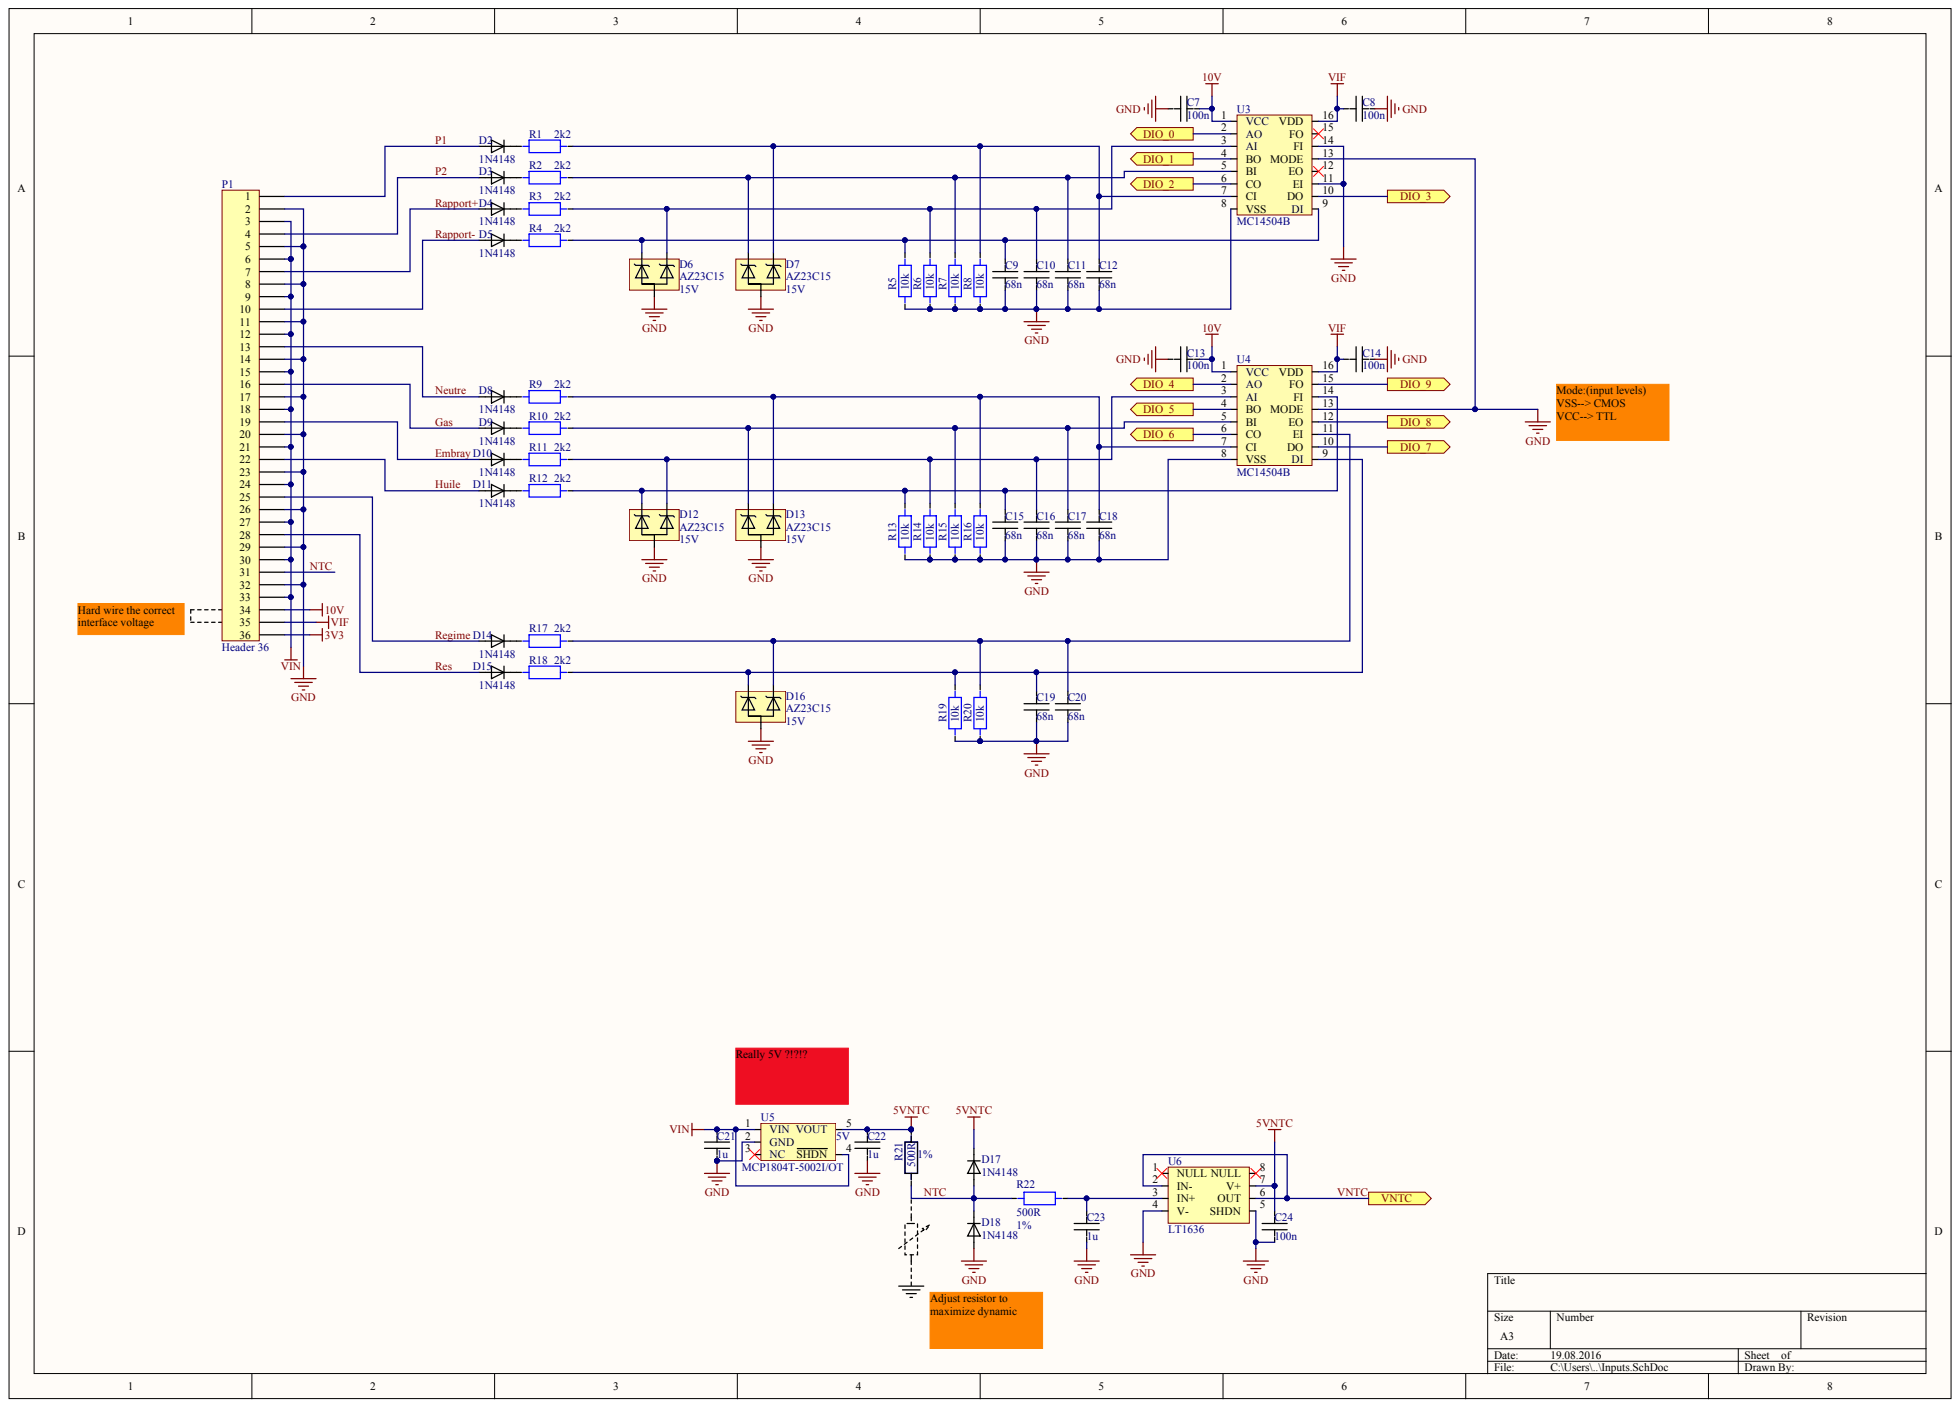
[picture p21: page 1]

Rapport-

Gas

Hard wire the correct
interface voltage

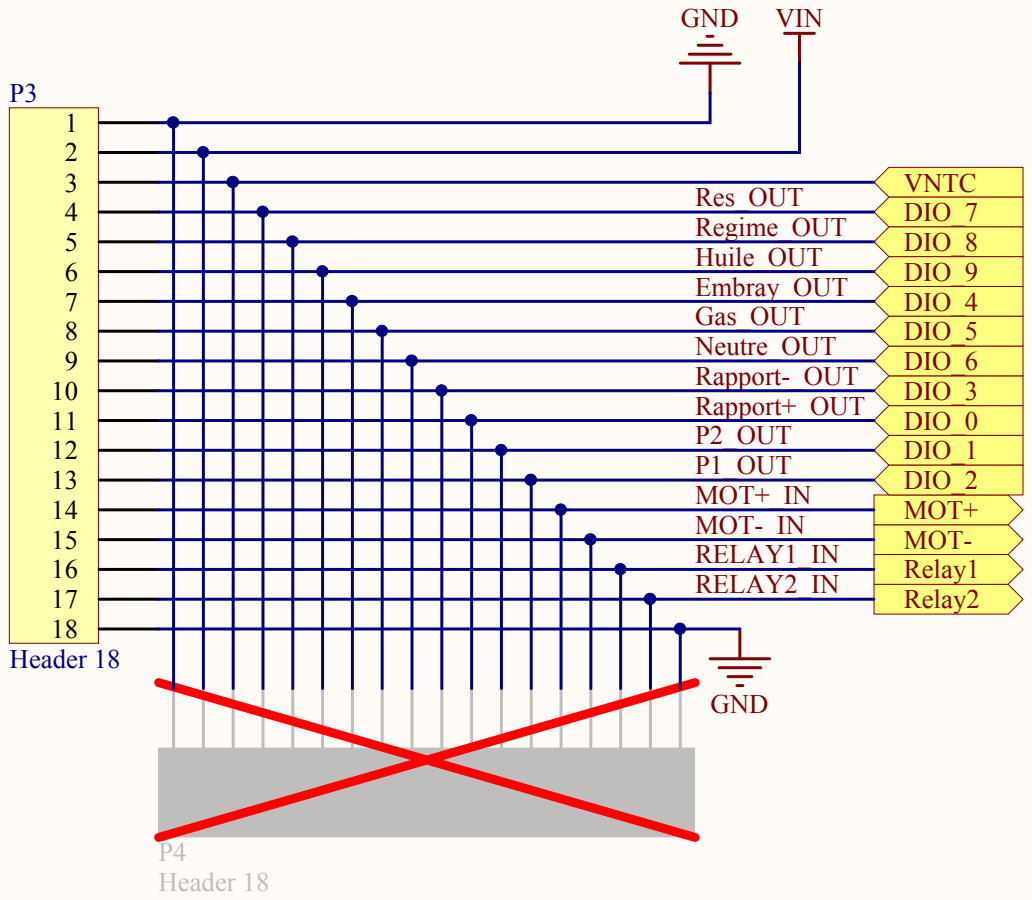
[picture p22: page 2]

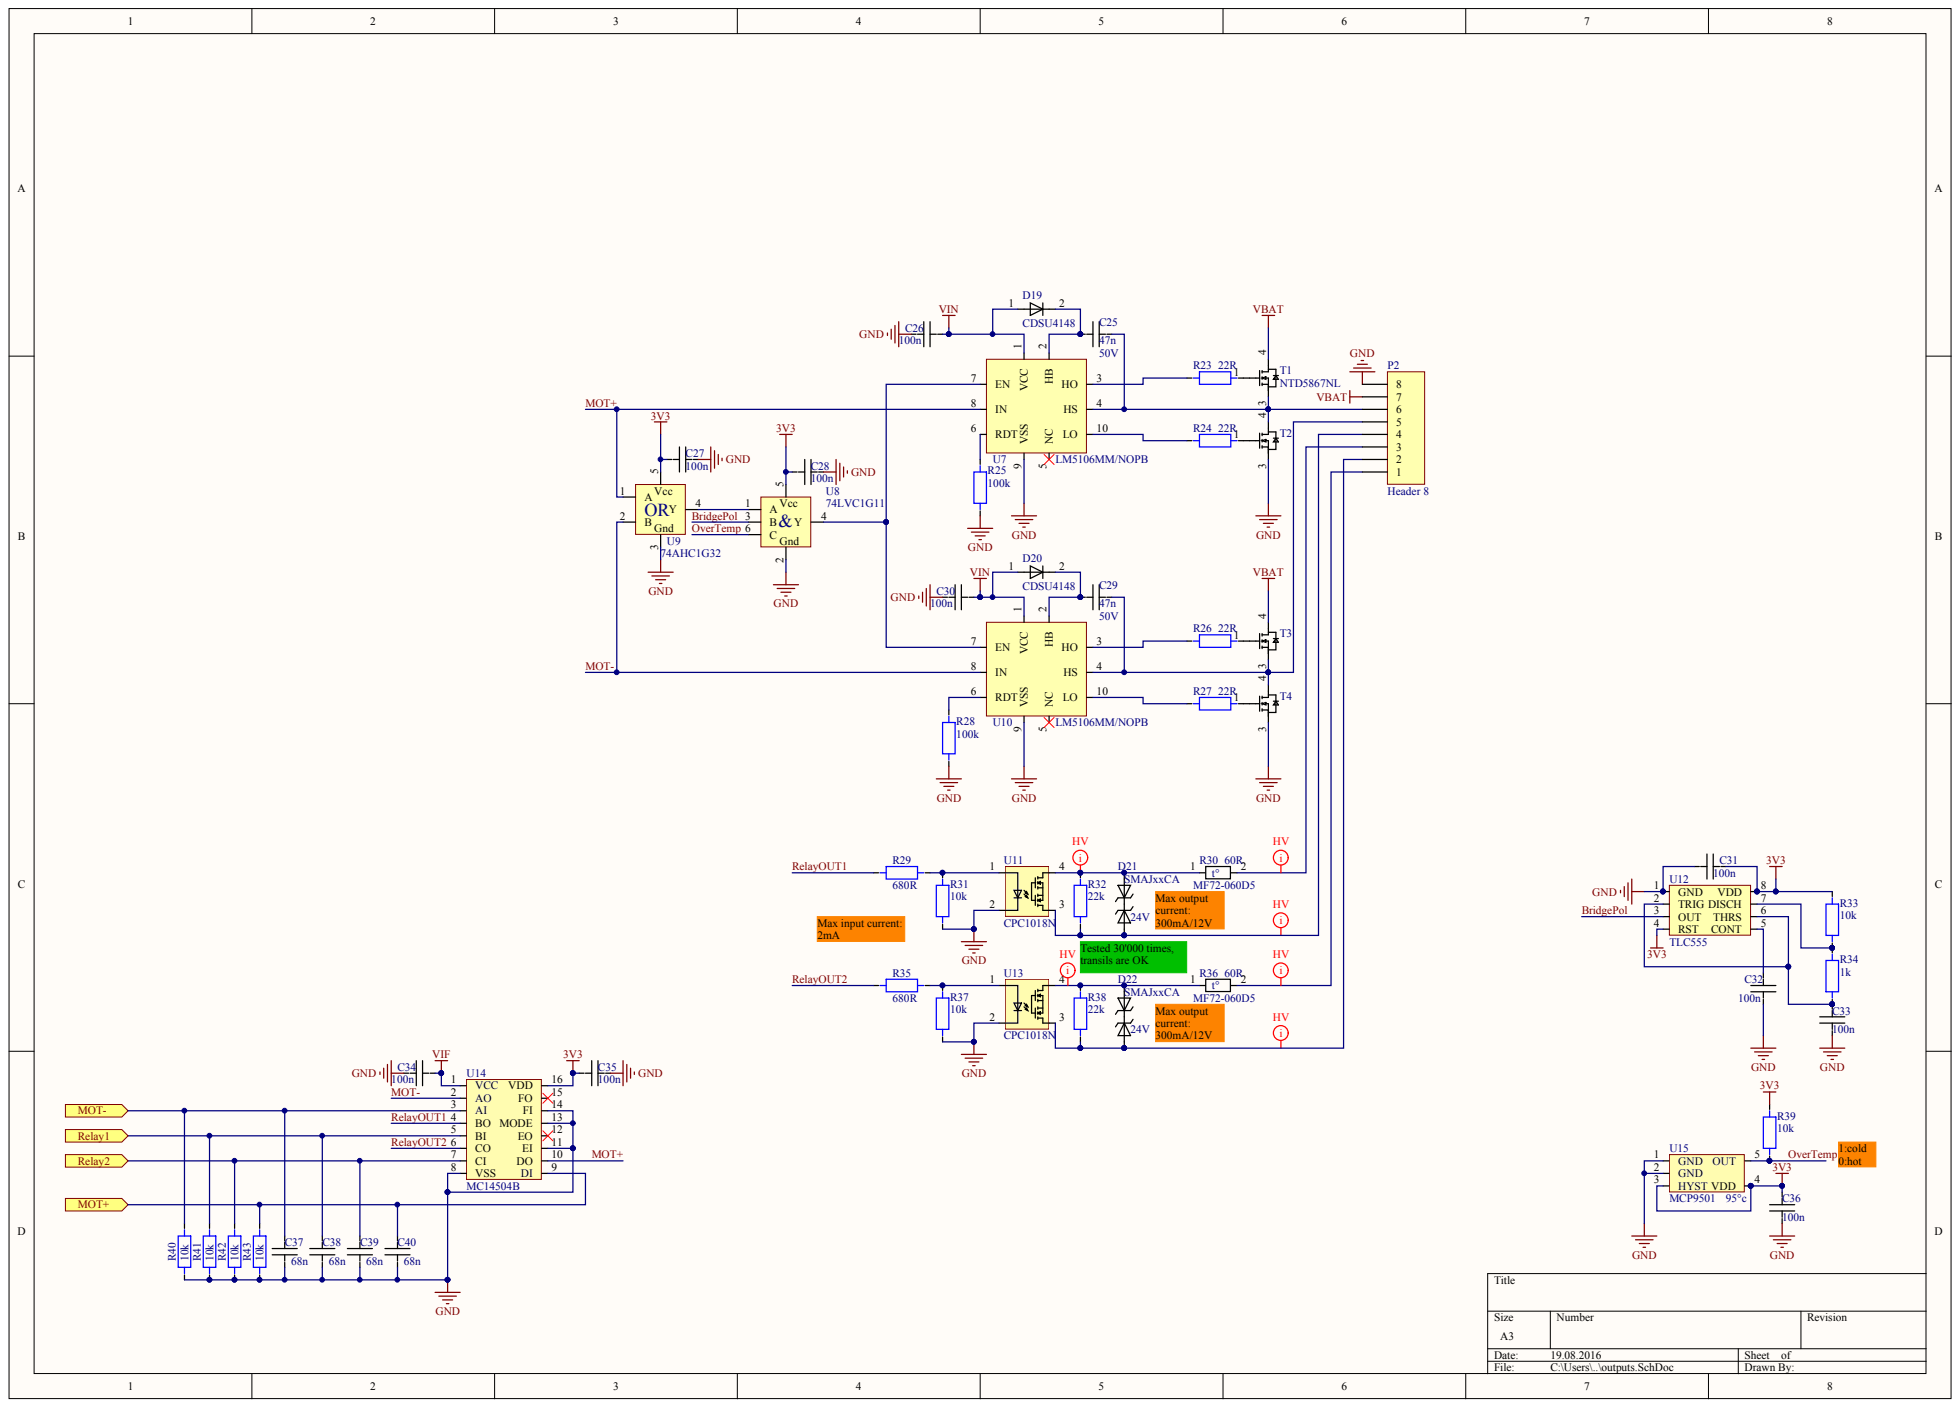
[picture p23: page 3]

T RIG OUT THR S RST CONT

Tested 30'000 times, transils are OK | 300mA/12V Max output

HV HVi

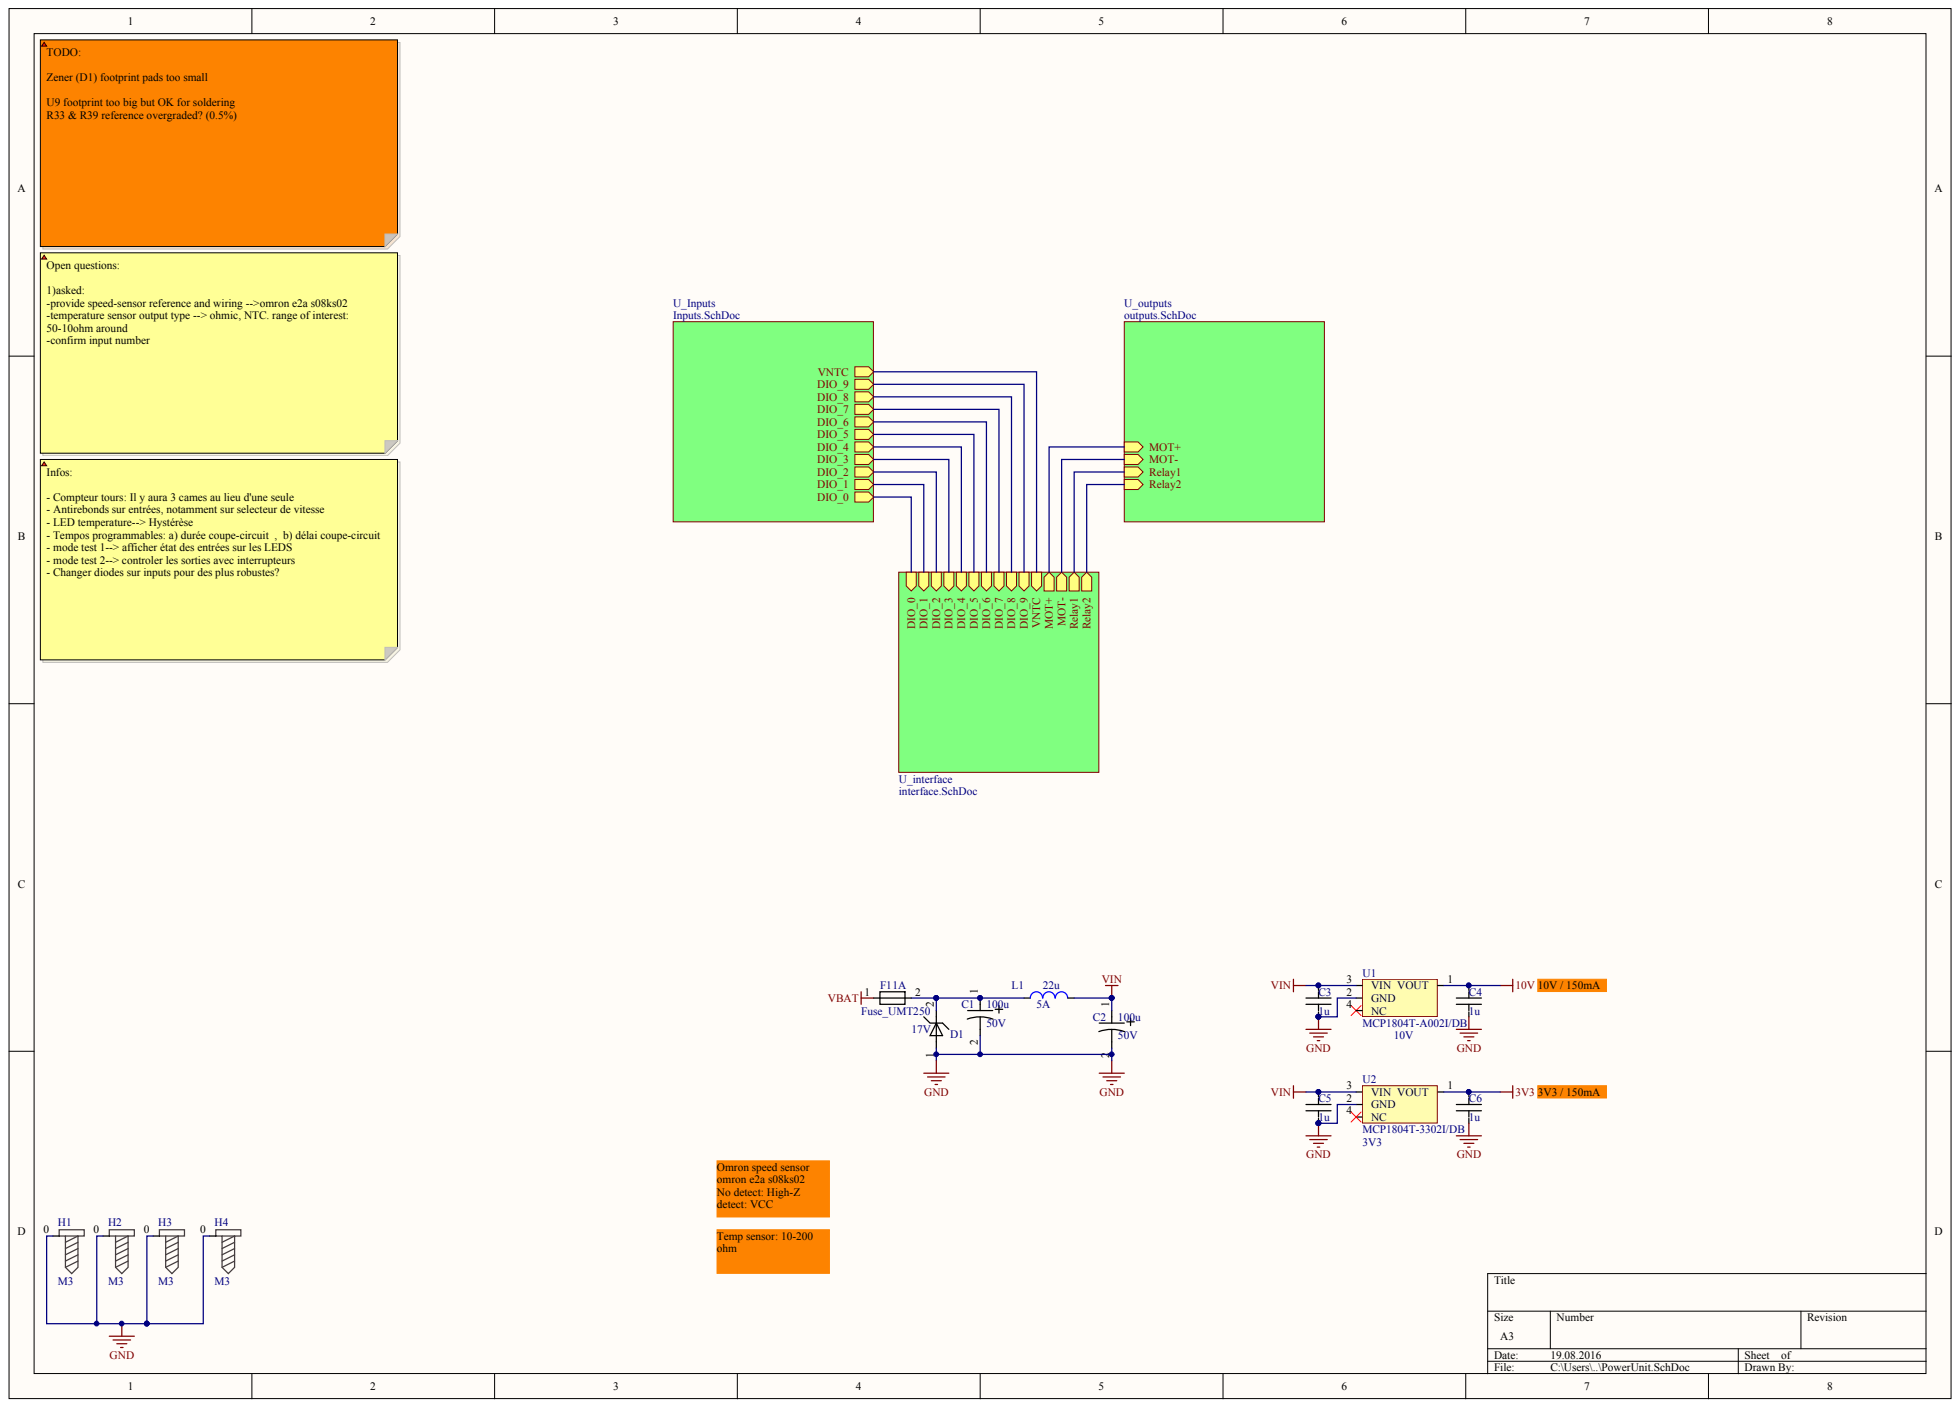
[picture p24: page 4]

-confirm input number TODO: Zener (D1) footprint pads too small

U9 footprint too big but OK for soldering R33 & R39 reference overgraded? (0.5%)

1)asked:
-provide speed-sensor reference and wiring -->omron e2a s08ks02
-temperature sensor output type --> ohmic, NT
50-10ohm around

- Compteur tours: Il y aura 3 cames au lieu d'une seule
- Antirebonds sur entrées, notamment sur selecteur de vites
- Tempos programmables: a) durée coupe-circuit , b) délai coupe-circuit
- mode test 1--> afficher état des entrées sur les L
- mode test 2--> controler les sorties avec interrupteurs
- Changer diodes sur inputs pour des plus robustes

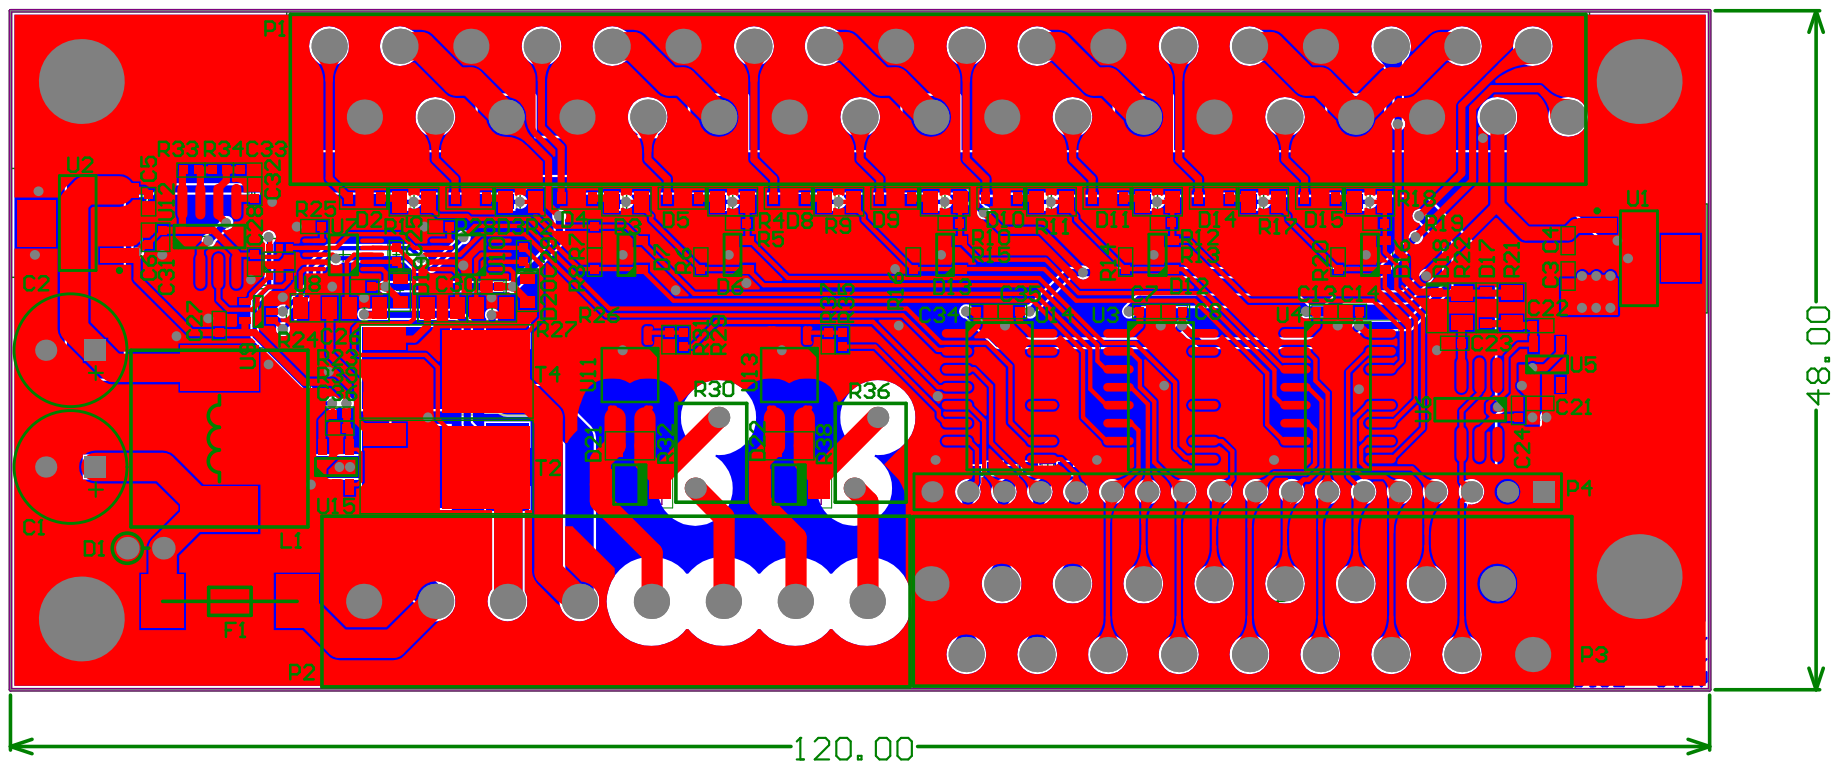
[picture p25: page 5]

Designator | Description | Manufacturer | Manufacturer PartNum | Digikey ref | Quantity
C1, C2 | | Nichicon | UVR1H101MPD1TD | 493-5916-1-ND | 2
C3, C4, C5, C6, C21, C22, C23 | | Murata | GRM155R61E105MA12 D | 490-10018-1-ND | 7
C7, C8, C13, C14, C24, C26, C27, C28, C30, C31, C32, C33, C34, C35, C36 | | TDK Corp. | C1005X5R1E104K050BC | 445-4964-1-ND | 15
C9, C10, C11, C12, C15, C16, C17, C18, C19, C20, C37, C38, C39, C40 | | Samsung | CL10B683KB8NNNC | 1276-1814-1-ND | 14
C25, C29 | | Murata | GRM155R71H473KE14D | 490-10702-1-ND | 2
D1 | | ON Semi | 1N5354BG | 1N5354BGOS-ND | 1
D2, D3, D4, D5, D8, D9, D10, D11, D14, D15, D17, D18 | | Micro Commercial Co | 1N4148WX-TP | 1N4148WXTPMSCT-ND | 12
D6, D7, D12, D13, D16 | DIODE ZENER ARRAY 15V SOT23-3 | Diodes Inc. | AZ23C15-7-F | AZ23C15-FDICT-ND | 5
D19, D20 | | Comchip Tech. | CDSU4148 | 641-1001-1-ND | 2
D21, D22 | SMAJ Transient Voltage Suppressor Diode Series | Littelfuse Inc | SMAJ24CA | SMAJ24CALFCT-ND | 2
F1 | | Schurter Inc | 3403.0166.11 | 486-1247-ND | 1
L1 | | Wurth Electronics Inc | 7447709220 | 732-1243-1-ND | 1
P1 | Header, 36-Pin | Phoenix Contact | 1990164 | 277-1810-ND | 1
P2 | Header, 8-Pin | Phoenix | 1869279 | 277-5855-ND | 1
P3 | Header, 10-Pin | Phoenix | 1990164 | 277-1810-ND | 1
R1, R2, R3, R4, R9, R10, R11, R12, R17, R18 | | Yageo | RC0805JR-072K2L | 311-2.2KARCT-ND | 10
R5, R6, R7, R8, R13, R14, R15, R16, R19, R20, R31, R37, R40, R41, R42, R43 | | Panasonic | ERJ-2RKF1002X | P10.0KLCT-ND | 16
R21, R22 | | Yageo | RC0805FR-07510RL | 311-510CRCT-ND | 2
R23, R24, R26, R27 | | Panasonic | ERJ-6ENF22R0V | P22.0CCT-ND | 4
R25, R28 | | Susumu | RR0510P-104-D | RR05P100KDCT-ND | 2
R29, R35 | | Panasonic | ERJ-2RKF6800X | P680LCT-ND | 2
R30, R36 | | Cantherm | MF72-060D5 | 317-1146-ND | 2
R32, R38 | | Rohm Semi | ESR10EZPJ223 | RHM22KKCT-ND | 2
R33, R39 | | Susumu | RR0510P-103-D | RR05P10.0KDCT-ND | 2
R34 | | Rohm Semi | MCR01MRTF1001 | RHM1.00KCDCT-ND | 1
T1, T2, T3, T4 | | On Semi | NTD5867NLT4G | NTD5867NLT4GOSCT-ND | 4
U1 | IC REG LDO 10V 0.15A SOT223-3 | Microchip | MCP1804T-A002I/DB | MCP1804T-A002I/DBCT-ND | 1
U2 | IC REG LDO 3.3V 0.15A SOT223-3 | Microchip | MCP1804T-3302I/DB | MCP1804T-3302I/DBCT-ND | 1
U3, U4, U14 | IC LEVEL SHIFTER HEX 16-SOIC | On Semi | MC14504BDG | MC14504BDGOS-ND | 3
U5 | IC REG LDO 5V 0.15A SOT23-5 | Microchip | MCP1804T-5002I/OT | MCP1804T-5002I/OTCT-ND | 1
U6 | IC OPAMP GP 220KHZ RRO 8SO SHTDN | Linear Technology | LT1636CS8#PBF | LT1636CS8#PBF-ND | 1
U7, U10 | | Texas Intruments | LM5106MM/NOPB | LM5106MM/NOPBCT-ND | 2
U8 | IC GATE AND 1CH 3-INP SOT-363 | Diodes Inc. | 74LVC1G11DW-7 | 74LVC1G11DW-7CT-ND | 1
U9 | | Diodes Inc. | 74AHC1G32SE-7 | 74AHC1G32SE-7DICT-ND | 1
U11, U13 | | IXYS Integrated | CPC1018NTR | CLA225CT-ND | 2
U12 | IC OSC SGL TIMER 2.1MHZ 8-SOIC | Texas Intruments | TLC555CDR | 296-1336-1-ND | 1
U15 | | Microchip | MCP9501PT-095E/OT | MCP9501PT-095E/OTCT-N | 1

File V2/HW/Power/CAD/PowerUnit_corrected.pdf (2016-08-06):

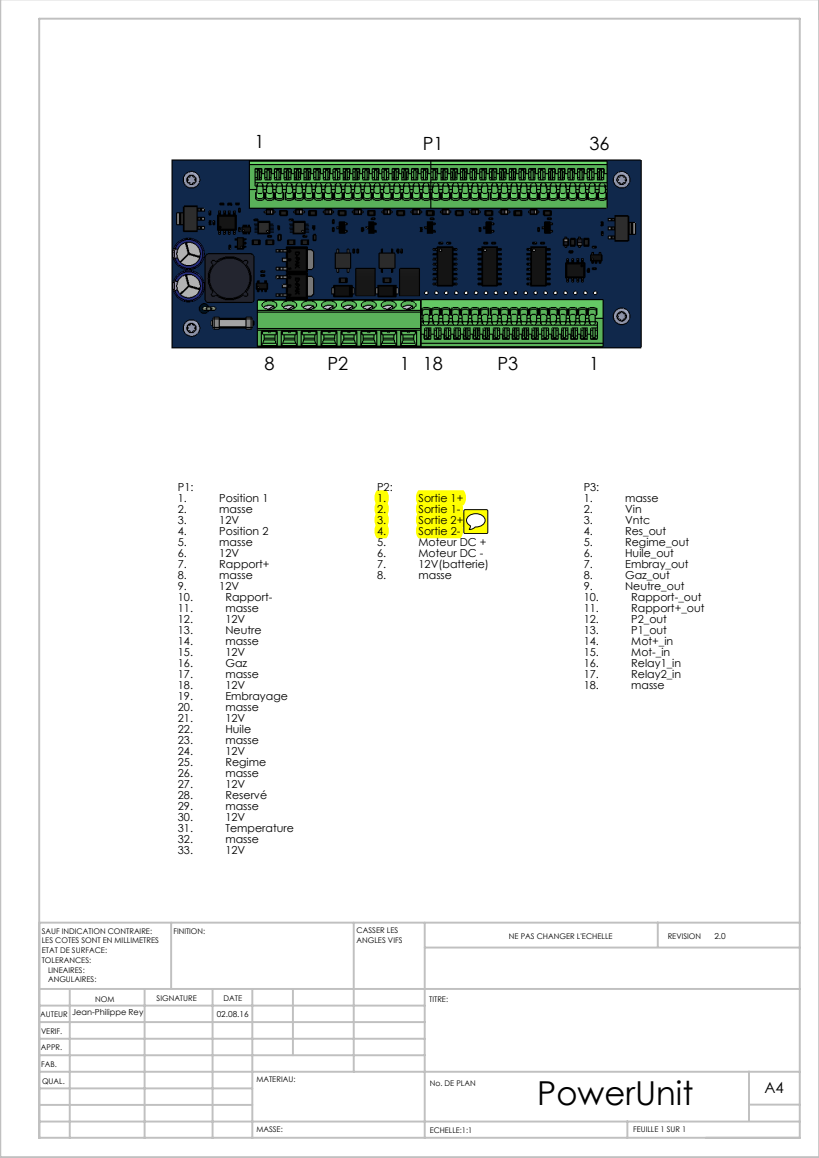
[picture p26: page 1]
1. Position 1 2. masse 3. 12V 4. Position 2 5. masse 6. 12V 7. Rapport+ 8. masse 9. 12V 10. Rapport- 11. masse 12. 12V 13. Neutre 14. masse 15. 12V 16. Gaz 17. masse 18. 12V 19. Embrayage 20. masse 21. 12V 22. Huile 23. masse 24. 12V 25. Regime 26. masse 27. 12V 28. Reservé 29. masse 30. 12V 31. Temperature 32. masse 33. 12V; 1. Sortie 1+ 2. Sortie 1- 3. Sortie 2+ 4. Sortie 2- 5. Moteur DC + 6. Moteur DC - 7. 12V(batterie) 8. masse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

LES COTES SONT EN MILLIMETRES
ETAT DE SURFACE:
TOLERANCES:
LINEAIRES:
ANGULAIRES:

NOM | SIGNATURE | DATE | | | | TITRE:
QUAL. | | | | MATERIAU: | PowerUnit MASSE: No. DE PLAN | A4

AUTEUR | Jean-Philippe Rey | | 02.08.16
VERIF.
APPR.
FAB.

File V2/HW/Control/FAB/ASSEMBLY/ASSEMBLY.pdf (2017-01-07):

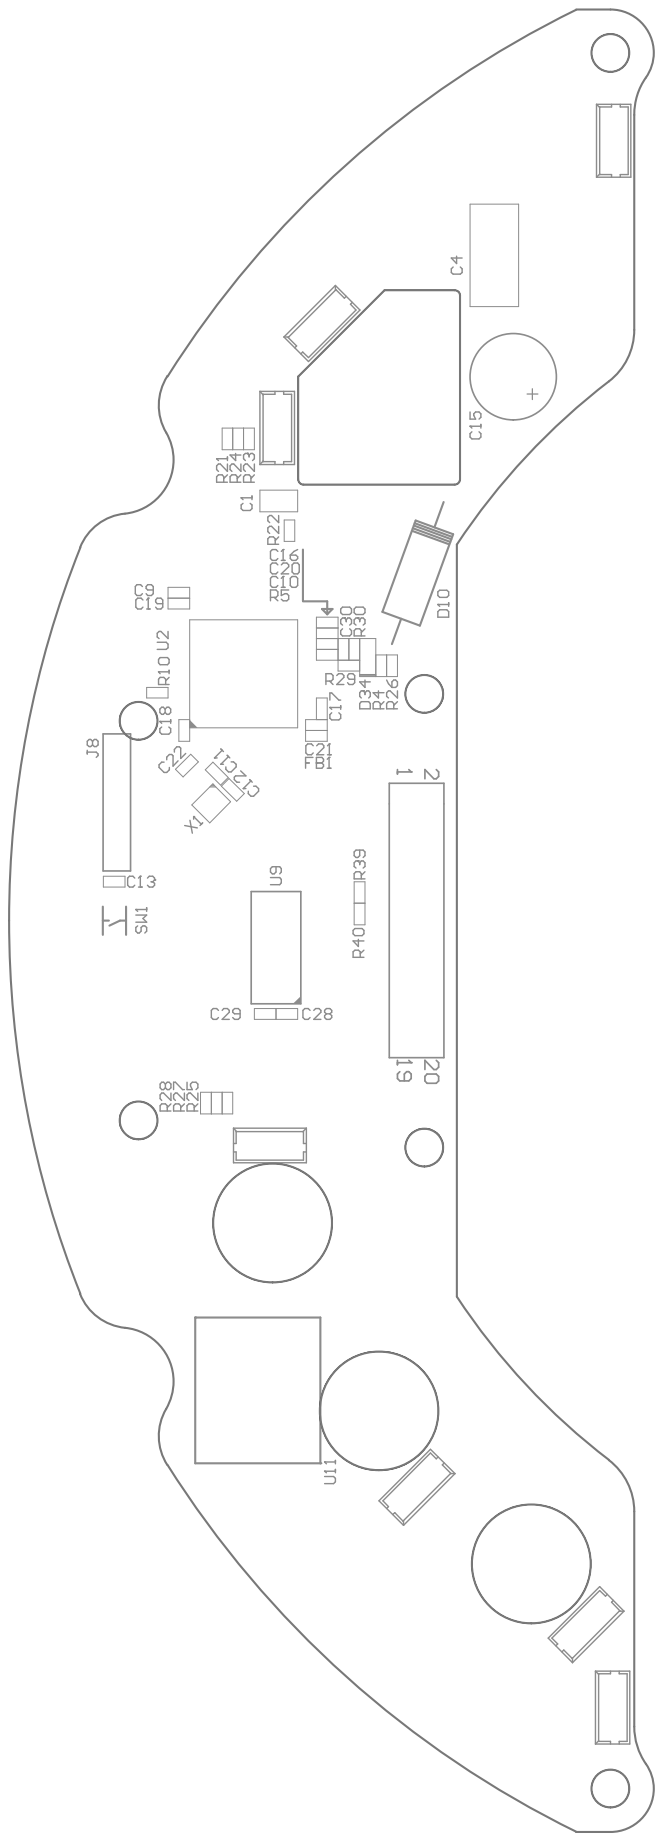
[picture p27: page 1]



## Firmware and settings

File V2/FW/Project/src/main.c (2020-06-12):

#include "main.h"
#include "stm32f2xx_it.h"

#define UID_ADDRESS_BASE (uint8_t*)(0x1FFF7A10)
#define UID_BYTE_SIZE   (12)

//#define FLASH_REINIT
//#define FAKE_ENGINE_SPEED_DATA
uint8_t UID[8];
uint8_t NXS_UID[12];
uint8_t NXS_EUI64[8];

//applications
xTaskHandle AppTaskHandle,ConfigTaskHandle,PeriodicTaskHandle,DiagnosticTaskHandle;
SemaphoreHandle_t MainAppMutex;
SemaphoreHandle_t MainConfigMutex;
SemaphoreHandle_t MainDiagMutex;

//application modes
uint8_t MainMode=MainMode_Init;

//other variables
uint8_t Vreg_based_LED=0;
uint8_t str[300];
uint16_t PotMinimumValueForAutoMode=0;//unit: rpm
uint32_t BlankingTime_ms=0;//unit: millisecond
EventGroupHandle_t CU_Inputs_EventGroup;

//shouldn't be here logically but easier to implement
uint8_t GetPotMinimumValueForAutoMode(void)
{
	return PotMinimumValueForAutoMode;
}

uint32_t GetBlankingTime_ms(void)
{
	return BlankingTime_ms;
}

uint8_t MainAppGetMode(void)
{
  return MainMode;
}

uint8_t MainAppChangeMode(uint8_t Mode)
{
  //take MainAppMutex first
  if( xSemaphoreTake( MainAppMutex, ( TickType_t ) 1000 ) != pdTRUE )
  {
    return 1;
  }
  //then take MainConfigMutex too
  if( xSemaphoreTake( MainConfigMutex, ( TickType_t ) 1000 ) != pdTRUE )
  {
    xSemaphoreGive(MainAppMutex);
    return 1;
  }
  //finally take MainDiagMutex too
  if( xSemaphoreTake( MainDiagMutex, ( TickType_t ) 1000 ) != pdTRUE )
  {
    xSemaphoreGive(MainConfigMutex);
    xSemaphoreGive(MainAppMutex);
    return 1;
  }
  
  switch(Mode)
  {
  case MainMode_App:
    MainMode=MainMode_App;
    break;
  case MainMode_Diagnostic:
    CU_LEDsSetIntensity(80);     //set luminosity to 80%. On exit, system is rebooted, intensity is read from FLASH
    MainMode=MainMode_Diagnostic;
    break;
  case MainMode_Configuration:
    CU_LEDsSetIntensity(100);     //set luminosity to 100%. Exact intensity is restored when exiting CONF mode
    MainMode=MainMode_Configuration;
    break;
  default:break;
  }
  //release mutexes 
  xSemaphoreGive(MainAppMutex);
  xSemaphoreGive(MainConfigMutex);
  xSemaphoreGive(MainDiagMutex);
  return 0;
}

void ToggleLed1(void * pvParameters)
{
  uint32_t led_value=1, direction=0, max=20;
  for( ;; )
  {
    if(direction)
    {
      if(led_value<max)
        led_value++;
      else
        direction=0;      
    }
    else
    {
      
      if(led_value>1)
        led_value--;
      else
        direction=1;    
    }
    CU_LEDOn(LED_BLUE);
    vTaskDelay(led_value);
    CU_LEDOff(LED_BLUE);
    vTaskDelay(max-led_value);
  }
}

void F3000_Conf(void * pvParameters)
{
  uint8_t state=0;
  uint8_t varNum=0;
  uint8_t paramValue=0;
  uint32_t ledIntensity=0;
  uint32_t Seg7Intensity=0;
  uint32_t PotMinValueForAutoMode=0;//range: 1- MAX LEDS
  uint32_t BlankingTime=0;//ms
  while(1)
  {
    if(MainMode==MainMode_Configuration)
    {
      //take MainConfigMutex 
      if( xSemaphoreTake( MainConfigMutex, ( TickType_t ) 100 ) != pdTRUE )
      {
        continue;
      }
      
      switch(state)
      {
      case 0:
        SEG7_Set(SEG7_C);
        vTaskDelay(1000);
        while(CU_GetNeutralButton())
          vTaskDelay(20);
        state=1;
        break;
      case 1:
        varNum=bargraph_getPotValue();
        if(varNum>9)
          varNum=9;
        bargraph_MaskSet(0x01<<(varNum-1));
        SEG7_Set(varNum);
        if(CU_GetNeutralButton())
        {
          state=2;
          while(CU_GetNeutralButton())
            vTaskDelay(20);
        }
        break;
      case 2:
        SEG7_Set(varNum);
        SEG7_EnableDot(1);
        bargraph_DisplayPotValue();
        paramValue=bargraph_getPotValue();
        switch(varNum)
        {
        case 6:// set the potentiometer threshold minimum value for AUTO mode
		  if(CU_GetNeutralButton())
		  {
			PotMinValueForAutoMode=(uint32_t)paramValue;
			PC_SetParam((uint8_t*)&PotMinValueForAutoMode,"AUTO_GU_MT");
			while(CU_GetNeutralButton())
			  vTaskDelay(20);
			state=1;
		  }
	  break;
        case 7:// set 7seg intensity
          if(CU_GetNeutralButton())
          {
            Seg7Intensity=(uint32_t)((float)paramValue*4.7619);
            PC_SetParam((uint8_t*)&Seg7Intensity,"SEG7_I");
            while(CU_GetNeutralButton())
              vTaskDelay(20);
            state=1;
          }
          break;
        case 8:// set the blanking time between two GEAR UP
          if(CU_GetNeutralButton())
          {
        	  BlankingTime=(uint32_t)paramValue;
        	  BlankingTime=BlankingTime*50;//50ms per LED
              PC_SetParam((uint8_t*)&BlankingTime,"AUTO_GU_BT");
              while(CU_GetNeutralButton())
                vTaskDelay(20);
            state=1;
          }
          break;
        case 9:// set LEDs intensity
          if(CU_GetNeutralButton())
          {
            ledIntensity=(uint32_t)((float)paramValue*4.7619);
            PC_SetParam((uint8_t*)&ledIntensity,"LED_I");
            while(CU_GetNeutralButton())
              vTaskDelay(20);
            state=1;
          }
          break;
        default:
          SEG7_Set(SEG7_E);
          vTaskDelay(500);
          state=1;//no parameter found, return to parameter selection
          break;
        }
        break;
      default:break;
      }
      
      //release MainConfigMutex 
      xSemaphoreGive(MainConfigMutex);
      if(CU_GetStopButton())
      {
        state=0;
#ifdef RESET_CU_WHEN_EXITING_CONFIGURATION_MODE
        NVIC_SystemReset();
#endif /* RESET_CU_WHEN_EXITING_CONFIGURATION_MODE */
        /*MainAppChangeMode(MainMode_App);
        PC_GetParam((uint8_t*)&ledIntensity,"LED_I");
        CU_LEDsSetIntensity( (float)ledIntensity );

        PC_GetParam((uint8_t*)&Seg7Intensity,"SEG7_I");
        CU_SEG7sSetIntensity( (float)Seg7Intensity );

        PC_GetParam((uint8_t*)&PotMinValueForAutoMode,"AUTO_GU_MT");//automatic mode, gear UP,minimum pot threshold
        PotMinimumValueForAutoMode=PotMinValueForAutoMode;

        PC_GetParam((uint8_t*)&BlankingTime_ms,"AUTO_GU_BT");//automatic mode, gear UP, blanking time
        BlankingTime_ms=BlankingTime;*/
      }
      vTaskDelay(20);
    }
    else
      vTaskDelay(300);
    
  }
}

void F3000_Diag(void * pvParameters)
{
  uint8_t dummy=0;
  while(1)
  {
    if(MainMode==MainMode_Diagnostic)
    {
      SEG7_Set(SEG7_d);
      //take MainDiagMutex 
      if( xSemaphoreTake( MainDiagMutex, ( TickType_t ) 100 ) != pdTRUE )
      {
        continue;
      }
      
      bargraph_MaskSet(CU_ReadInputsRaw());
     
      //release MainDiagMutex 
      xSemaphoreGive(MainDiagMutex);
      
      if(CU_GetStopButton())
      {
        MainAppChangeMode(MainMode_App);
#ifdef RESET_CU_WHEN_EXITING_DIAGNOSTIC_MODE
        NVIC_SystemReset();
#endif /* RESET_CU_WHEN_EXITING_DIAGNOSTIC_MODE */
      }
      vTaskDelay(20);
    }
    else
      vTaskDelay(300);
  }
}

void F3000_Periodic(void * pvParameters)
{
#ifdef FAKE_ENGINE_SPEED_DATA
  uint8_t updown=1;
  uint32_t userRPM=500;
#endif /* FAKE_ENGINE_SPEED_DATA */
  uint32_t i=0;
  uint8_t GearMode;
  uint8_t PotValue=1;
  uint8_t PotValueMinScaled=0;
  uint8_t DelayBetweenTwoGearUp=0;
  while(1)
  {
    vTaskDelay(100);
    
    //handle App, Conf or Diag modes
    if(CU_GetNeutralButton())
    {
      i=20;
      while(i && CU_GetNeutralButton())
      {
        vTaskDelay(100);
        i--;
      }
      if(CU_GetNeutralButton())
      {
        if(MainMode==MainMode_App)
        {
          if(MainAppChangeMode(MainMode_Diagnostic))
          {
            //problem
          }
          //bargraph_Set(1,7,0);
        }
        else if(MainMode==MainMode_Diagnostic)
        {
          if(MainAppChangeMode(MainMode_Configuration))
          {
            //problem
          }
          //bargraph_Set(7,14,0);
        }
        else if(MainMode==MainMode_Configuration)
        {
          if(MainAppChangeMode(MainMode_App))
          {
            //problem
          }
        }
      }
      else
      {
        gear_toNeutral();
      }
    }

    //check MODE buttons
    GearMode=CU_GetMode();
    gear_SetMode(GearMode);
    Indicator_LED_Mode_Set(GearMode);

    /* check Pot value for AUTO mode */
    PotValue=bargraph_getPotValue();
    PotValueMinScaled=GetPotMinimumValueForAutoMode();
    if(PotValue<PotValueMinScaled )
      PotValue=PotValueMinScaled;
    if(GearMode==CU_Mode_Auto && CU_RPMToBargraph()>=PotValue)
    {
      if( (gear_getPosition()<gear_pos_5) && (gear_getPosition()!=gear_pos_N) && CU_GetGazInput() && !CU_GetEmbrayInput() && !DelayBetweenTwoGearUp)
      {
        gear_increase();
        DelayBetweenTwoGearUp=DELAYBETWEEN2GEARUP_100MS;
      }
    }
    if(DelayBetweenTwoGearUp)
      DelayBetweenTwoGearUp--;

    //handle temperature sensor
    Indicator_LED_Temp_Set(tempSensor_Get_State());
    Vreg_based_LED=((uint8_t)(tempSensor_Get_Temp()*4.2))%22;

    //handle OIL sensor
    if(CU_GetOilWarning())
      Indicator_LED_OIL_Set();
    else
      Indicator_LED_OIL_Reset();
    
    //handle bargraph
#ifdef FAKE_ENGINE_SPEED_DATA
    if(MainMode==MainMode_App)
    {
      bargraph_Set(1,CU_UserInputToBargraph(userRPM));
      if(updown)
      {
        userRPM+=75;
        if(userRPM>CU_RPM_MAX)
          updown=0;
      }
      else
      {
        userRPM-=75;
        if(userRPM<CU_RPM_MIN)
          updown=1;
      }
    }
#else /*FAKE_ENGINE_SPEED_DATA */
    if(MainMode==MainMode_App)
      bargraph_Set(1,CU_RPMToBargraph());
#endif /* FAKE_ENGINE_SPEED_DATA */

    //handle STOP button
    if(CU_GetStopButton())
      CU_STOP_On();
    else
      CU_STOP_Off();
    
    //Neutral LED 
    if(gear_getPosition()==gear_pos_N)
      Indicator_LED_N_Set();
    else
      Indicator_LED_N_Reset();
  }
}

extern EventGroupHandle_t gear_Events;
void PALG_Gear_cb(void){
  xEventGroupSetBitsFromISR(gear_Events,GEAR_EVENT_DECREASE,0);
}

void PALD_Gear_cb(void){
  xEventGroupSetBitsFromISR(gear_Events,GEAR_EVENT_INCREASE,0);
}

void F3000_App(void * pvParameters)
{
  uint8_t err=0;
  uint32_t param;
  if(CU_Inputs_EventGroup==NULL)
    err++;
  
  DebouncerInit(CU_Inputs_EventGroup);
  //uint32_t InputMask,GPIO_TypeDef* GPIO,uint16_t Pin,uint8_t Edge,uint32_t Event,uint32_t DebounceTime_ms
  DebouncerAddInput(CU_INPUT_EVENT_CAME_BIT,CAME_INPUT_GPIO_PORT,CAME_INPUT_PIN,DEBOUNCER_INT_EDGE_RISING,CU_INPUT_EVENT_CAME_BIT,0,10);
  
  /* debounce and calls respective callbacks conditionally on PALG and PALD */
  DebouncerAddInput(CU_INPUT_EVENT_PALG_BIT,PALG_INPUT_GPIO_PORT,PALG_INPUT_PIN,DEBOUNCER_INT_EDGE_FALLING,CU_INPUT_EVENT_PALG_BIT,PALG_Gear_cb,100);
  DebouncerAddInput(CU_INPUT_EVENT_PALD_BIT,PALD_INPUT_GPIO_PORT,PALD_INPUT_PIN,DEBOUNCER_INT_EDGE_FALLING,CU_INPUT_EVENT_PALD_BIT,PALD_Gear_cb,100);
  
  /* debounce and generate Events on Rapport+ and Rapport- signals*/
  DebouncerAddInput(CU_INPUT_EVENT_RAPPORTp_BIT,RAPPORTp_INPUT_GPIO_PORT,RAPPORTp_INPUT_PIN,DEBOUNCER_INT_EDGE_RISING,CU_INPUT_EVENT_RAPPORTp_BIT,NULL,10);
  DebouncerAddInput(CU_INPUT_EVENT_RAPPORTm_BIT,RAPPORTm_INPUT_GPIO_PORT,RAPPORTm_INPUT_PIN,DEBOUNCER_INT_EDGE_RISING,CU_INPUT_EVENT_RAPPORTm_BIT,NULL,10);
  

  while(!err)
  {
    if(MainMode==MainMode_App)
    {
      //take MainAppMutex first
      if( xSemaphoreTake( MainAppMutex, ( TickType_t ) 100 ) != pdTRUE )
      {
        continue;
      }
      
      /*if(CU_GetNeutralButton())
      {
       gear_toNeutral();
      }*/
      //LEDbuffer_MaskSet(0xFFFFFFFFFFFF);
      //LEDbuffer_refresh(0);
      //release MainAppMutex 
      xSemaphoreGive(MainAppMutex);
      vTaskDelay(50);
    }
    else
      vTaskDelay(200);
    
  }
  while(1)
    vTaskDelay(1000);
}

uint8_t F3000CLIInterpreter(uint8_t *raw)
{
  uint8_t *cmd=raw;
  if(strstr(cmd,"SYS -g BuildDate")>0)
  {
    CLI_Output(__DATE__":"__TIME__);
    return 0;
  }
  if(strstr(cmd,"SYS -g Temp")>0)
  {
    CLI_Output("Temp: not yet measured");
    return 0;
  }
  if(strstr(cmd,"SYS -s LEDLum")>0)
  {
    uint32_t lum=0;
    cmd=strstr(cmd,"SYS -s LEDLum");
    if(strstr(cmd,"=")>0)
    {
      cmd=strstr(cmd,"=")+1;
      if(cmd[0]>='0' && cmd[0]<='9')
      {
        if(cmd[1]>='0' && cmd[1]<='9')
        {
          if(cmd[2]>='0' && cmd[2]<='9')
          {
            lum+=(cmd[0]-'0')*100;
            lum+=(cmd[1]-'0')*10;
            lum+=cmd[2]-'0';
          }
          else
          {
            lum+=(cmd[0]-'0')*10;
            lum+=cmd[1]-'0';
          }
        }
        else
          lum+=cmd[0]-'0';
      }
      if(lum>0 && lum<=100)
      {
        PC_SetParam((uint8_t*)&lum,"LED_I");
        PC_GetParam((uint8_t*)&lum,"LED_I");
        CU_LEDsSetIntensity( ((float)lum) );
        LEDbuffer_refresh(1);
        sprintf(str,"LED luminosity set to %3i [%]",lum);
        CLI_Output(str);
      }
    }
    return 0;
  }
  if(strstr(cmd,"SYS -s SegLum")>0)
    {
      uint32_t lum=0;
      cmd=strstr(cmd,"SYS -s SegLum");
      if(strstr(cmd,"=")>0)
      {
        cmd=strstr(cmd,"=")+1;
        if(cmd[0]>='0' && cmd[0]<='9')
        {
          if(cmd[1]>='0' && cmd[1]<='9')
          {
            if(cmd[2]>='0' && cmd[2]<='9')
            {
              lum+=(cmd[0]-'0')*100;
              lum+=(cmd[1]-'0')*10;
              lum+=cmd[2]-'0';
            }
            else
            {
              lum+=(cmd[0]-'0')*10;
              lum+=cmd[1]-'0';
            }
          }
          else
            lum+=cmd[0]-'0';
        }
        if(lum>0 && lum<=100)
        {
          PC_SetParam((uint8_t*)&lum,"SEG7_I");
          PC_GetParam((uint8_t*)&lum,"SEG7_I");
          CU_SEG7sSetIntensity( ((float)lum) );
          LEDbuffer_refresh(1);
          sprintf(str,"7SEG luminosity set to %3i [%]",lum);
          CLI_Output(str);
        }
      }
      return 0;
    }
  else if(strstr(cmd,"SYS -r")>0)
  {
    CLI_Output("Rebooting... Please unconnect and reconnect Bluetooth app");
    vTaskDelay(2000);
    NVIC_SystemReset();
  }
  else if(strstr(cmd,"GEAR -s UP")>0)
  {
    gear_increase();
    CLI_Output("GEAR: OK");
  }
  else if(strstr(cmd,"GEAR -s DOWN")>0)
  {
    gear_decrease();
    CLI_Output("GEAR: OK");
  }
  else if(strstr(cmd,"GEAR -s NEUTRAL")>0)
  {
    gear_toNeutral();
    CLI_Output("GEAR: OK");
  }
  else
  {
    CLI_Output("\r\nCommand ERROR");
    return 1;
  }
  CLI_Output("\r\nDone");
  return 0;
}

void F3000_Init(void * pvParameters)
{
  uint32_t param;

  UID_Init(UID_ADDRESS_BASE,UID_BYTE_SIZE);
  UID_getUID(UID);
  UID_getNXSFormat(NXS_UID);
  EUI64_getNXSFormat(NXS_EUI64);
  //LEDs_Init();
  LEDbuffer_Init();
  timer_init();
  ITS_Init(NULL,0);
  tempSensor_Init(NULL);
  bargraph_Init();
  CU_LEDsInit();
  //CU_IOInit(); already done earlier in F3000_System_Start
  vTaskDelay(200);//wait a little bit in order to let flash be ready
  if(flash_init())
     console_log("can't init flash");
  if( PC_Init() )
    console_log("can't init Parameter Collection. Flash problem?");
#ifdef FLASH_REINIT
  /* Here are the default Parameter values to be initially stored in flash */
  param=30;
  PC_SetParam((uint8_t*)&param,"LED_I");

  param=30;
  PC_SetParam((uint8_t*)&param,"SEG7_I");

  param=5000;
  PC_SetParam((uint8_t*)&param,"AUTO_GU_MT");// see detail inPC_Init() function

  param=500;//millisecond
  PC_SetParam((uint8_t*)&param,"AUTO_GU_BT"); //see detail in PC_Init() function
#endif /* FLASH_REINIT */
  vTaskDelay(200);//safe wait before reading flash memory
  PC_GetParam((uint8_t*)&param,"LED_I");
  CU_LEDsSetIntensity( (float)param );

  PC_GetParam((uint8_t*)&param,"SEG7_I");
  CU_SEG7sSetIntensity( (float)param );

  PC_GetParam((uint8_t*)&param,"AUTO_GU_MT");
  PotMinimumValueForAutoMode=(uint16_t)param;

  PC_GetParam((uint8_t*)&param,"AUTO_GU_BT");
  BlankingTime_ms=param;
  if(gear_Init())
  {
    console_log("can't init GearBox");
  }
  //Applications mutexes
  MainAppMutex = xSemaphoreCreateMutex();
  MainConfigMutex = xSemaphoreCreateMutex();
  MainDiagMutex = xSemaphoreCreateMutex();

  //events
  CU_Inputs_EventGroup=xEventGroupCreate();
  
  STBT_Init(COM1);
  console_Init(STBT_ConsoleOutput);
  CLI_Init(console_log,F3000CLIInterpreter);
  
  /* WELCOME SEQUENCE */
  uint8_t a,b;
  bargraph_NegMaskState(0);
  a=1;
  b=1;
  /* everything OFF */
  LEDbuffer_MaskReset(0xFFFFFFFFFFFF);
  LEDbuffer_refresh(0);
  
  /* simulate engine speed increase */
  while(b<=21)
  {
    bargraph_Set(a,b);
    b++;
    vTaskDelay(15);
  }
  
  /* everything ON */
  LEDbuffer_MaskSet(0xFFFFFFFFFFFF);
  LEDbuffer_refresh(0);
  vTaskDelay(700);
  

  /* Everything OFF */
  LEDbuffer_MaskReset(0xFFFFFFFFFFFF);
  LEDbuffer_refresh(0);
  
  /* Simulate engine speed decrease */
  while(b>0)
  {
    bargraph_Set(a,b);
    b--;
    vTaskDelay(15);
  }
  bargraph_NegMaskState(1);
  
  /********************************************************************************/
  /*//TODO: Remove this debug code
  uint8_t buf[1];
  PCA9952_LED_Intensity_Control(PCA9952_MAIN_ADDR,0x1000,SEG7_SEG_INTENSITY);
  PCA9952_LED_Control(PCA9952_MAIN_ADDR,0x1000);
  PCA9952_LED_Intensity_Control(PCA9952_MAIN_ADDR,0x1000,50);
  PCA9952_write_reg(PCA9952_MAIN_ADDR,REG_GRPPWM,0xFF);
  PCA9952_write_reg(PCA9952_MAIN_ADDR,REG_GRPPWM,127);
  PCA9952_write_reg(PCA9952_MAIN_ADDR,REG_GRPPWM,0xFF);
  PCA9952_LED_Intensity_Control(PCA9952_MAIN_ADDR,0x1000,100);
  PCA9952_write_reg(PCA9952_MAIN_ADDR,REG_MODE2,0x25);
  PCA9952_read_reg(PCA9952_MAIN_ADDR,REG_MODE2,buf,1);
  PCA9952_write_reg(PCA9952_MAIN_ADDR,REG_MODE2,0x05);
  PCA9952_read_reg(PCA9952_MAIN_ADDR,REG_MODE2,buf,1);
  PCA9952_read_reg(PCA9952_MAIN_ADDR,REG_MODE2,buf,1);
  while(1);*/

  /* restore normal tasks */
  vTaskResume(ConfigTaskHandle);
  vTaskResume(DiagnosticTaskHandle);
  vTaskResume(PeriodicTaskHandle);
  vTaskResume(AppTaskHandle);
  MainMode=MainMode_App;
  vTaskDelete(NULL);
}

void F3000_System_Start(void)
{
  //init IO before anything else in order to avoid outputs to be floating
  CU_IOInit();
  //xTaskCreate(ToggleLed1, "LED1", configMINIMAL_STACK_SIZE, NULL, LED_TASK_PRIO, NULL);
  xTaskCreate(F3000_App, "Application", configMINIMAL_STACK_SIZE, NULL, LED_TASK_PRIO, &AppTaskHandle);
  xTaskCreate(F3000_Periodic, "PeriodicTask", configMINIMAL_STACK_SIZE, NULL, LED_TASK_PRIO, &PeriodicTaskHandle);
  xTaskCreate(F3000_Conf, "Config", configMINIMAL_STACK_SIZE, NULL, LED_TASK_PRIO, &ConfigTaskHandle);
  xTaskCreate(F3000_Diag, "Diag", configMINIMAL_STACK_SIZE, NULL, LED_TASK_PRIO, &DiagnosticTaskHandle);
  vTaskSuspend(ConfigTaskHandle);
  vTaskSuspend(DiagnosticTaskHandle);
  vTaskSuspend(PeriodicTaskHandle);
  vTaskSuspend(AppTaskHandle);
  xTaskCreate(F3000_Init, "F3000Init", configMINIMAL_STACK_SIZE, NULL, LED_TASK_PRIO, NULL);
  vTaskStartScheduler();
}

void main(void)
{
  /* System function that updates the SystemCoreClock variable. */

  SystemCoreClockUpdate();
  NVIC_PriorityGroupConfig( NVIC_PriorityGroup_4 );//no bits of sub-priority. Only preemption priorities are used
  F3000_System_Start();
  
  /* We should never get here as control is now taken by the scheduler */
  for( ;; );
}

void vApplicationMallocFailedHook(void)
{
  uint8_t i=0; 
  console_log("\nERROR: Failed to allocate a ressource!\n");
  /*while(1)
  {
    ;
  }*/
  i++;
}

void vApplicationStackOverflowHook( xTaskHandle xTask,
                                    signed portCHAR *pcTaskName )
{
  console_log("\nERROR: Stack overflow!\n");
  while(1);
}

void assert_failed(uint8_t* file, uint32_t line)
{
  uint8_t i=1;
  console_log("\nAssert failed. File: ");
  console_log(file);
  sprintf(str,"\nLine: %i",line);
  console_log(str);
  while(i)
  {
    vTaskDelay(100);
  }
} 

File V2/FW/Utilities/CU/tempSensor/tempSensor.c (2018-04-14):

#include "tempSensor.h"
#include "ADC.h"

void tempSensor_Monitor_callback(uint16_t value);

void (*tempSensor_cb)(float)=0;

#define TEMPSENSOR_ADC_ACCU_SIZE 10
uint16_t tempSensor_ADCAccu[TEMPSENSOR_ADC_ACCU_SIZE];
uint8_t tempSensor_ADCAccuPtr=0;
float tempSensor_currentValue=0;//defined as the input voltage (on header). range: [0..5]V
uint8_t tempSensor_currentState=TempSensor_Cold;//can be cold, medium or hot


void tempSensor_Init(void (*callback)(float))
{
  
  ADC_LowLevelInit();
  //callback init
  if(callback!=NULL)
  {
    tempSensor_cb=callback;
    //ADC_RegisterCallback(TEMP_IN_ADC_CHANNEL,tempSensor_cb);
  }
  else
    ADC_RegisterCallback(TEMP_IN_ADC_CHANNEL,tempSensor_Monitor_callback);
}

uint8_t tempSensor_Get_State(void)
{
  return tempSensor_currentState;
}

float tempSensor_Get_Temp(void)
{
  return tempSensor_currentValue;
}

void tempSensor_Monitor_callback(uint16_t value)
{
  uint32_t tempSensor_Accu=0;
  float tempSensor_value;
  uint8_t i;
  
  tempSensor_ADCAccu[tempSensor_ADCAccuPtr++]=value;
  if(tempSensor_ADCAccuPtr>=TEMPSENSOR_ADC_ACCU_SIZE)
  {
    tempSensor_ADCAccuPtr=0;
    for(i=0;i<TEMPSENSOR_ADC_ACCU_SIZE;i++)
      tempSensor_Accu+=tempSensor_ADCAccu[i];
    tempSensor_value=(((float)tempSensor_Accu)/((float)TEMPSENSOR_ADC_ACCU_SIZE));
    tempSensor_currentValue=tempSensor_value*0.001245;//conversion to be fine-tuned
    

    //define temperature state
    if( tempSensor_currentValue>=TEMPSENSOR_THRESHOLD_1 )
      tempSensor_currentState=1;
    else if( tempSensor_currentValue>=TEMPSENSOR_THRESHOLD_2 && tempSensor_currentValue<TEMPSENSOR_THRESHOLD_1 )
      tempSensor_currentState=2;
    else if( tempSensor_currentValue>=TEMPSENSOR_THRESHOLD_3 && tempSensor_currentValue<TEMPSENSOR_THRESHOLD_2 )
      tempSensor_currentState=3;
    else if( tempSensor_currentValue>=TEMPSENSOR_THRESHOLD_4 && tempSensor_currentValue<TEMPSENSOR_THRESHOLD_3 )
      tempSensor_currentState=4;
    else if( tempSensor_currentValue>=TEMPSENSOR_THRESHOLD_5 && tempSensor_currentValue<TEMPSENSOR_THRESHOLD_4 )
      tempSensor_currentState=5;
    else if( tempSensor_currentValue>=TEMPSENSOR_THRESHOLD_6 && tempSensor_currentValue<TEMPSENSOR_THRESHOLD_5 )
      tempSensor_currentState=6;
    else 
      tempSensor_currentState=7;
  }
}

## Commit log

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2016-04-05 -Power outputs checked and reinforced with Power NTCs
    [PowerUnit.SchDoc]
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2016-04-06 - Added a fixed duty-cycling circuit for H-bridge
    [PowerUnit.SchDoc]
2016-04-06 - Added "Open questions" tracking box - Updated mapping between digital IO and level shifter
    [PowerUnit.SchDoc]
2016-04-06 - integrated infos from Julien - digital inputs have now a name
    [PowerUnit.SchDoc]
2016-04-07 - Added the 8th input on the Phoenix contact - Added a 3V3 regulator
    [PowerUnit.SchDoc]
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2016-04-08 - Added an input protection on VBAT - Added a conditioner-circuit for NTC measurement (+ dedicated LDO)
    [PowerUnit.SchDoc]
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2016-04-22 - Reorganized the schematics. Now we have separated sheets for Inputs, Outputs and Interface
    [Inputs.SchDoc, PowerUnit.PrjPCB, PowerUnit.SchDoc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]
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2016-04-22 - Added 2 digital inputs: "Regime" and "Res"(reservé) - Propagated those 2 new signals up to the output interface
    [Inputs.SchDoc, PowerUnit.SchDoc, interface.SchDoc]
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2016-05-04 - Added temporary headers - Added a lowpass capacitor on the VNTC - Study around the usage of an isolated DC/DC. Delta Electronics PG02S1212A (941-1181-ND) could be of interest
    [Inputs.SchDoc, PowerUnit.PrjPCB, PowerUnit.SchDoc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]
2016-05-12 - H-bridge GND to be replaced by BGND ?!? - Added a DC/DC - Added Control board V1 to GIT
    [F3000.PrjPCB, Inputs.SchDoc, PowerUnit.PcbDoc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]
2016-06-03 - Complete redesign without useless voltage isolators - NTC Analog front end optimized
    [Inputs.SchDoc, PowerUnit.PcbDoc, PowerUnit.SchDoc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]
2016-06-03 - Added digital inputs protection zener - Added voltage selector for the Interface
    [Inputs.SchDoc, PowerUnit.SchDoc]
2016-06-03 - Inputs.SchDoc and outputs.SchDoc nearly ready to route - Still need to adapt levels on ControlUnit-->PowerUnit (need to be flexible)
    [Inputs.SchDoc, PowerUnit.SchDoc, interface.SchDoc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]
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2016-06-13 - Added level translator for motor & opto outputs - Changed H-bridge VCC (is now VBAT)
    [PowerUnit.PcbDoc, outputs.SchDoc]
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2016-06-13 - Designators reseted, new annotatation - BOM references in progress (Manufacturer, Manufacturer part-number, Digikey-ref)
    [Inputs.SchDoc, PowerUnit.PcbDoc, PowerUnit.PrjPCB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]
2016-06-15 - 36-pos header (inputs) created and placed - 3d Sketch created for validation
    [Inputs.SchDoc, PowerUnit.PcbDoc, interface.SchDoc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]
2016-06-16 - Inputs are now normalized to 10V (instead of formerly 3V3 ) - Input Zener protection diodes fixed to 15V
    [Inputs.SchDoc, PowerUnit.PcbDoc]
2016-06-16 - signals from the power board going to control board are directly mapped on the header.
    [interface.SchDoc]
2016-06-16 -H-bridges VDD are now referenced on VIN -Logic level converter driving "outputs" is now MC14504 as well - Decoupling capacitors added to logic level converters and h-bridge drivers
    [Inputs.SchDoc, interface.SchDoc, outputs.SchDoc]
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2016-06-16 - Inputs lowpass capacitor footprints changed from 0402 to 0603 - Layout in progress
    [Inputs.SchDoc, outputs.SchDoc]
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2016-06-16 - Layout finished. No DRC errors. - Layout to be verified, especially Power nets and GND planes
    [PowerUnit.PrjPCB, outputs.SchDoc]
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2016-06-17 - Manufacturer details and Digikey References added on every component - BoM generated
    [Inputs.SchDoc, PowerUnit.PrjPCB, PowerUnit.xlsx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]
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2016-06-20 - Added a debug header (2.54mm) to ease interconnection with MCU platform - Layout checked - GERBERS generated
    [PowerUnit.GBL, PowerUnit.GBO, PowerUnit.GBP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]
2016-06-20 - Added teardrops on header nets - Updated BoM - PCB validated on EC checker
    [PowerUnit.SchDoc, PowerUnit.xlsx, interface.SchDoc]
2016-06-20 - Schematic done - PDF generated - BOM OK - GERBER generated - FAB folder created and fulfilled - V2 considered as stable and completed
    [Inputs.SchDoc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]
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2016-08-19 - input voltage protection zener footprint updated (hole size increased) - U9 footprint updated (SOT353 instead of SOT23-5) - FAB files updated
    [PowerUnit.GBL, PowerUnit.GBO, PowerUnit.GBP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]
2016-08-19 - Serigraphy updated - GERBER up to date - Layer stack up to date
    [PowerUnit.PrjPCB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]
2016-10-21 - Led drivers added - Most of the LEDs are added - Headers for switches are added - Power circuit in progress
    [ControlUnit.SchDoc, LEDs.SchDoc, PowerUnit.SchDoc]
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2016-10-22 - LED Temp_high changed from 3 to 5 mm - LEDs Mode updated(green-blue-green)
    [ControlUnit.PcbDoc, MCU.SchDoc]
2016-10-24 - Some manufacturer refs added (power) - main interface header added (still need to be correctly mapped). footprint centered - power supply partially placed - LEDs drivers partially placed. still nee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
    [ControlUnit.PcbDoc, LEDs.SchDoc, MCU.SchDoc]
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2016-11-25 - button headers placed and locked. - pin remap on some led-driver thus easing layout
    [ControlUnit.PcbDoc, LEDs.SchDoc]
2016-12-05 - LEDs remapped - STM32 placed - board cutout angles are now rounded - added filtering on 3V3 (L-C cell) - in progress: choose a good JTAG connector
    [ControlUnit.PcbDoc, LEDs.SchDoc, MCU.SchDoc]
2016-12-26 - placed Quartz, JTAG header - moved button connectors to bottom-side - added feature : powering through JTAG connector - updated Zener(protection) footprint
    [ControlUnit.PcbDoc, MCU.SchDoc]
2016-12-26 - decoupling capacitors placed (MCU) - I2C partially routed - SPI flash placed and routed - JTAG routed - RST button placed and routed
    [ControlUnit.PcbDoc, MCU.SchDoc]
2016-12-26 - stackup changed: standard 4layers (6C) stackup compliant with Eurocircuits proto service
    [ControlUnit.PcbDoc, MCU.SchDoc]
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2016-12-29 - added some level converters (interface to Power board=10V) - schematic +m routing to be completed
    [ControlUnit.PcbDoc, MCU.SchDoc]
2016-12-30 - added 3d model of the enclosure - remapped LED_Mode_x to ease routing
    [ControlUnit.PcbDoc, ControlUnit.SchDoc, LEDs.SchDoc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]
2016-12-30 - FW: prepared files for input description, added basic GEAR functions, added systick-timer (mono channel) - HW: level converter in progress
    [ControlUnit.PcbDoc, ControlUnit.SchDoc, LEDs.SchDoc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]
2017-01-02 -HW: level converters placed - layout finished. Waiting for Eurocircuits manufacturability report - GERBER generated
    [ControlUnit.PcbDoc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]
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2017-01-03 - Console IN/OUT OK over Bluetooth. - CLI bound to Bluetooth - Basic CLI implemented (get build date, soft reset the CU)
    [CU.c, STBT.c, main.c]
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2017-01-05 - Eurocircuit requirements are being taken into account (power planes clearance/minimum width). In progress...
    [ControlUnit.DWG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]
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2017-02-17 - Vreg (potentiometer value) is now used to display "speed limit before gear-up" in automatic driving mode - switching between app, diag and conf modes has been simplified (no more task suspend/resum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
    [CU.c, CU.h, gear.c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]
2017-02-20 - SPI flash driver in progress (unable to write right now. to be fixed)
    [CU.c, CU.h, main.c]
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2017-03-01 - Welcome sequence implemented - Diag mode: PALG and PALD display inverted (input active low)
    [CU.c, CU.h, main.c]
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2017-03-02 - gear UP and DOWN seems OK. - toNeutral seems to have problems. to be debugged direct on the real gearbox.
    [CU.c, gear.c, main.c]
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2017-03-24 - 7SEG intensity changed - Bargraph error corrected when in Diagnostic mode
    [CU.h, main.c]
2017-03-25 - Poll rate on CAME decreased to add reactivity - motor_stop() is now at state 1 instead of 0 (forces motor to break instead of free run) - When exiting neutral, modified conditions - Gaz managed whe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
    [CU.c, CU.h, gear.c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]
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2018-03-16 - LED intensity range: bug found and corrected. Maximum current can be achieved
    [ControlUnit.PcbDoc]
2018-03-23 Julien's request implemented: - when system thinks it is in Neutral but Neutral input is inactive, go to gear_lost state - potentiomenter is virtually floored when used in AUTO mode to gear up - prog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
    [CU.c, CU.h, gear.c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]
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2018-03-29 - CONFIG menu improved - SEG7 driver can now print "E" for "Error"
    [main.c]
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2018-04-14 commit after multiple changes on site: - temperature sensor calibration - regime adapted to came 3-poles - regime in auto mode limited by a parameter - delay between 2 GEAR UP, configurable - bug whe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
    [CU.c, CU.h, gear.c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]
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
